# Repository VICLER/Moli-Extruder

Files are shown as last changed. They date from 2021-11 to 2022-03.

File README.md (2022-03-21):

<h1 align="center">Moli Extruder</h1>
<p align="center">The most lightweight dual drive filament extruder based on BMG drive gears with 5:1 gear ratio.</p>

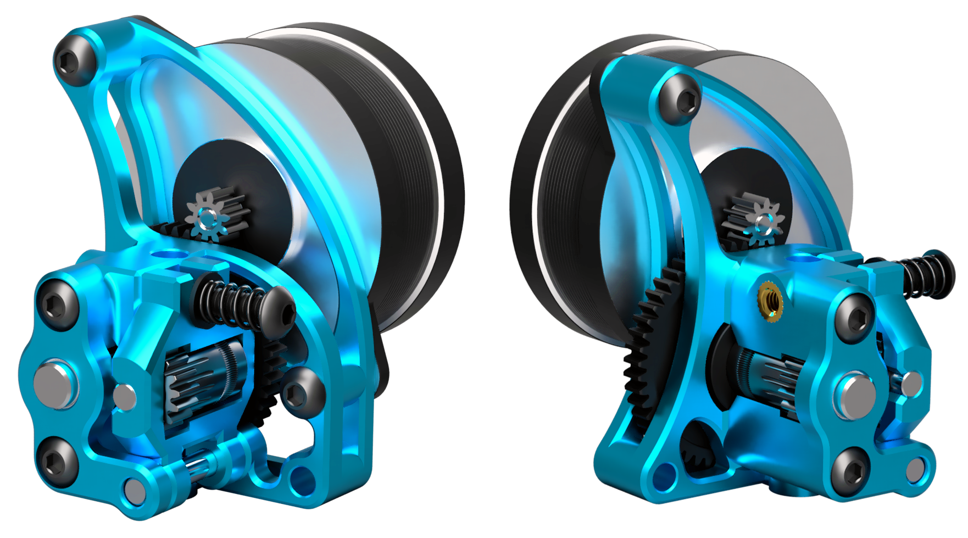
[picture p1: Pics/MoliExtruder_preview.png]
PROJECT_PHOTO


## Specs
- Outer dimensions (w/o motor) L×W×H: 37.2 × 28.2 × 48.7 (mm)
- Filament diameter: 1.75 mm
- Max feedrate: ~1200 mm/min
- Max flowrate: ~48 mm³/s
- Volume of all printed parts: ~6.14 cm³ (~63% less than Sailfin, ~55% less than Sherpa mini, ~52% less than HextrudORT and ~30% less than Sherpa micro extruder)
- Weight: <=25g (w/o motor). With LDO-36STH17-1004AHG: <=95g
- Mirrored version is also available

There are two versions for different types of BMG drive shaft available. They differ slightly, so check the measurements of your drive shaft and compare it with the CAD model  

This is a BETA release. Files, instructions, and other stuff might change!

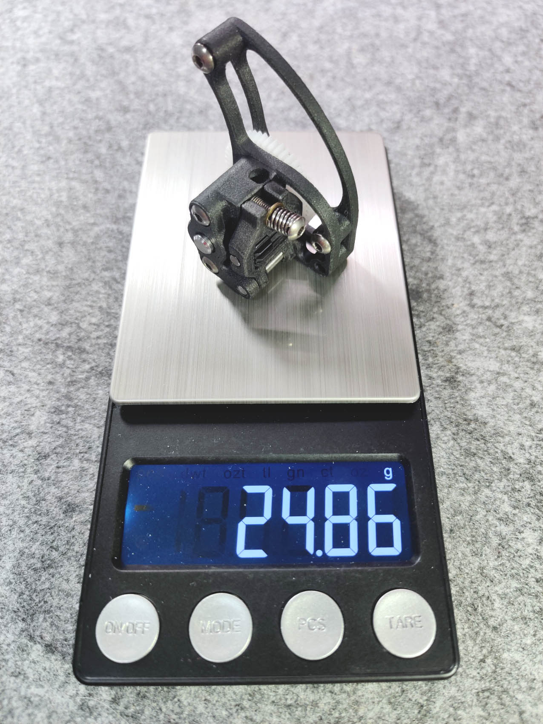
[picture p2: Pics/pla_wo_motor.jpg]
weight


## BOM
This extruder is designed to use Sherpa mini spare parts. Originally they are BMG dual drive extruder parts, but with one 3×20mm shaft instead of 3×32mm shaft. So you can buy original BMG dual drive spare parts and cut off the shaft by yourself.

- (1×) Motor [LDO-36STH 17/20mm](https://www.aliexpress.com/item/1005002899860754.html)  
- (1×) BMG internals [Recommended from Trianglelabs Store](https://www.aliexpress.com/item/4000021186440.html) or [Mellow Store](https://www.aliexpress.com/item/1005002254569027.html) (or [a bit cheaper, but not tested](https://www.aliexpress.com/item/1005003334389217.html))
- (1×) M3×18mm(optimal) or M3×16 screw
- (2×) M3×12mm screw
- (2×) M3×6mm  screw
- (1×) washer for M3 screw
- (1×) [compession spring](https://www.aliexpress.com/item/4000626844807.html). Wire diameter 0.7mm, outer diameter 5mm, length 10mm

## Print settings
Material: ABS or some high temp resistant filaments (like Extrudr Green-TEC PRO)  
Nozzle: <=0.4mm   
Walls:  3  
Infil:  100%  
Layer height: 0.1mm (optional 0.2mm first layer)

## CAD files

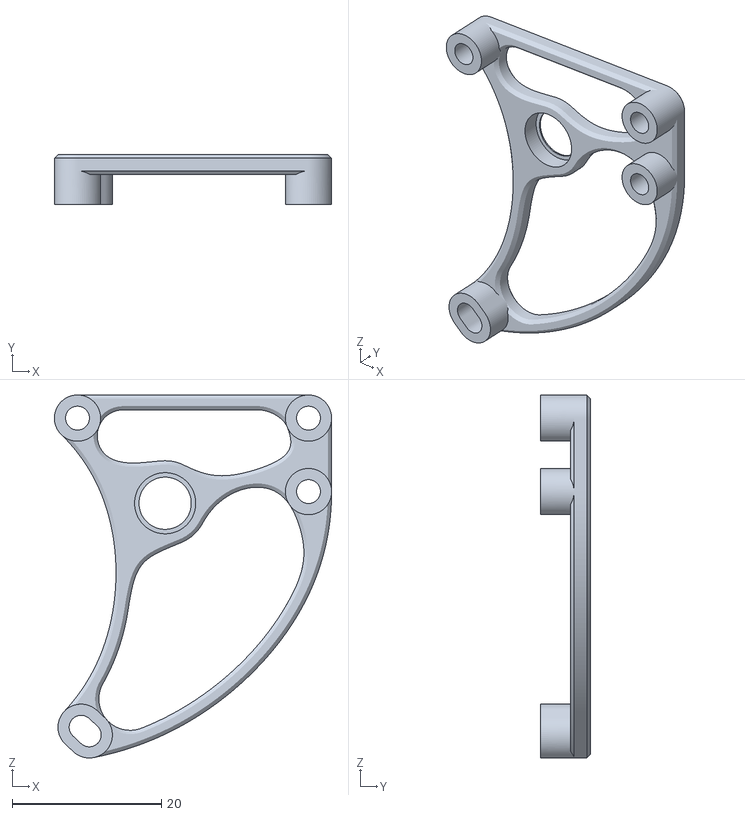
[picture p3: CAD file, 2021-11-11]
STL/BMG Fysetc Shaft/Mirror/MoliExtuder_bottom_mirror.stl
37.2 x 6.70 x 48.7

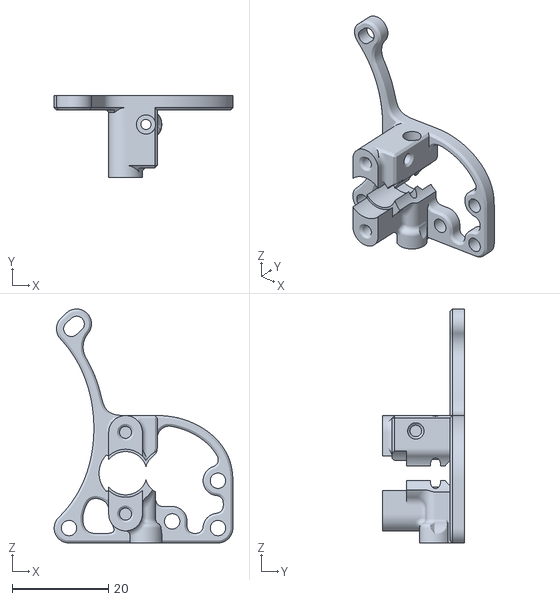
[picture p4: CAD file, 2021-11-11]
STL/BMG Fysetc Shaft/MoliExtruder_middle.stl
37.2 x 17.0 x 48.7

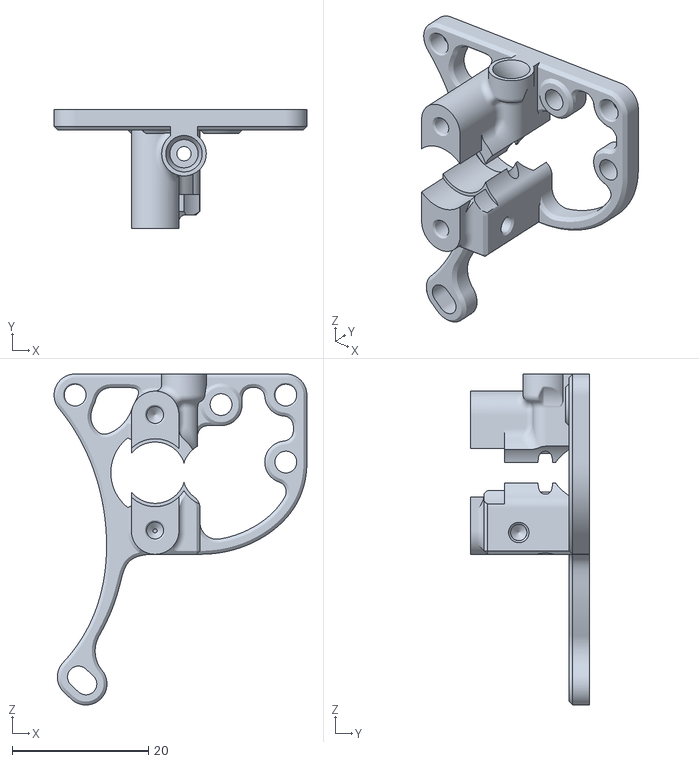
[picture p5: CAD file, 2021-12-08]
STL/BMG Shaft/Mirror/MoliExtruder_middle_mirror.stl
37.2 x 17.5 x 48.7

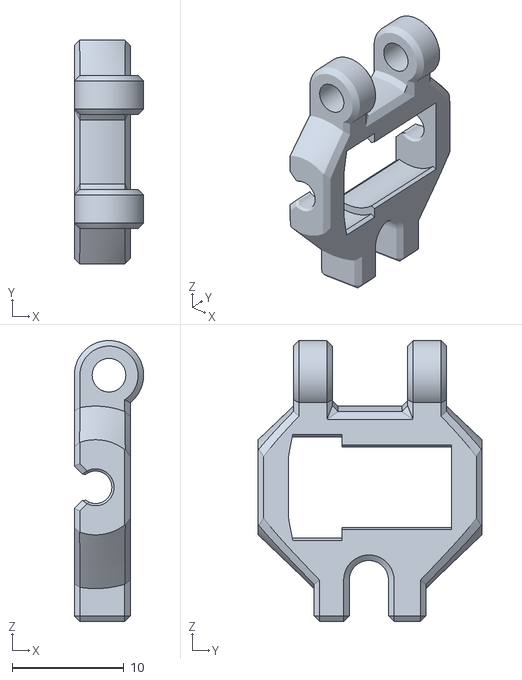
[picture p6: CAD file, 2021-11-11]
STL/BMG Fysetc Shaft/Mirror/MoliExtruder_arm_mirror.stl
6.20 x 20.0 x 25.1

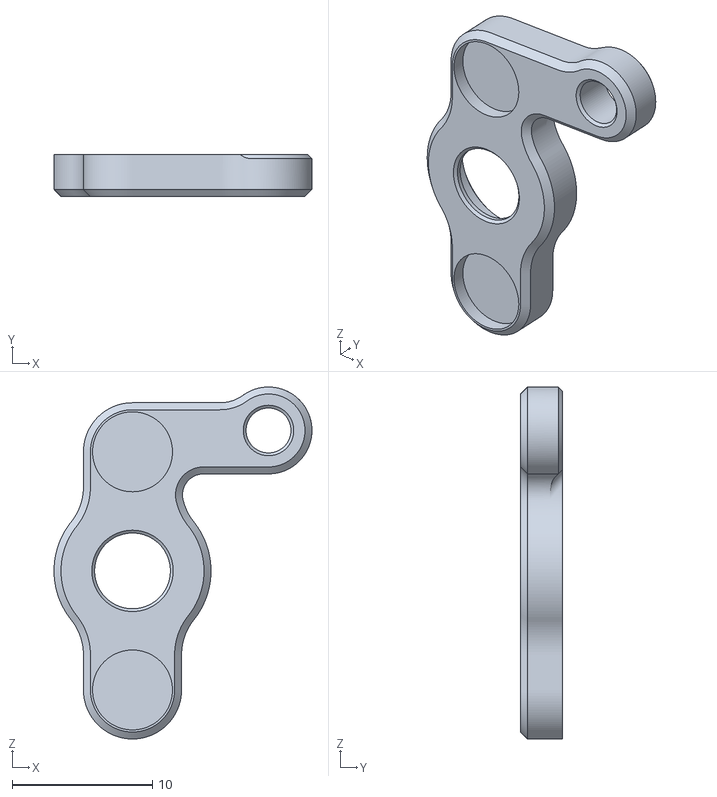
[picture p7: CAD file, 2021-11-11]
STL/BMG Shaft/Mirror/MoliExtruder_top_mirror.stl
18.4 x 3.00 x 25.1

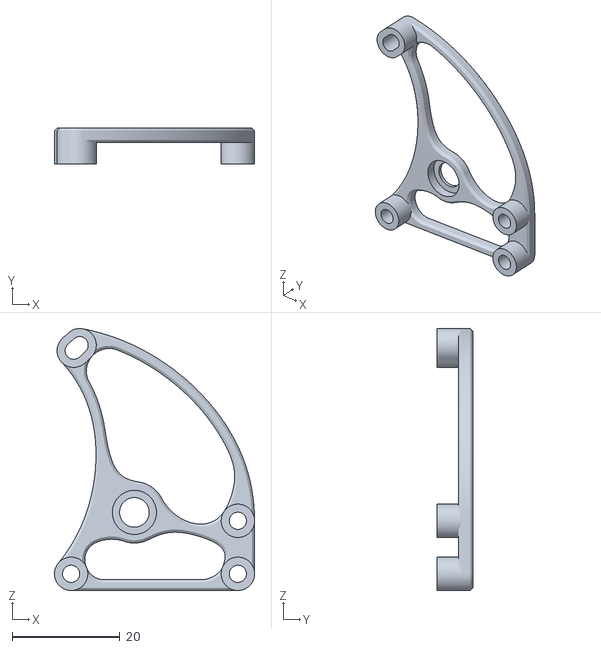
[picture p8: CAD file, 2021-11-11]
STL/BMG Shaft/MoliExtruder_bottom.stl
37.2 x 6.70 x 48.7

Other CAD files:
STL/BMG Shaft/MoliExtruder_middle.stl
STL/BMG Fysetc Shaft/MoliExtuder_bottom.stl
STL/BMG Shaft/Mirror/MoliExtruder_arm_mirror.stl
STL/BMG Shaft/MoliExtruder_arm.stl
STL/BMG Fysetc Shaft/Mirror/MoliExtruder_middle_mirror.stl
STL/BMG Fysetc Shaft/MoliExtruder_arm.stl
STL/BMG Fysetc Shaft/Mirror/MoliExtruder_top_mirror.stl
STL/BMG Fysetc Shaft/MoliExtruder_top.stl
STL/BMG Shaft/Mirror/MoliExtruder_bottom_mirror.stl
STL/BMG Shaft/MoliExtruder_top.stl

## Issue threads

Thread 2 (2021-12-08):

Extra ledge blocks the gear

fixid-pub, 2021-12-08:
File: STEP/BMG Shaft/Mirror/Middle
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

VICLER, 2021-12-08:
fixed!

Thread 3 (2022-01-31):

No screw holes in the top part

dolinenkov, 2022-01-31:
Hi!
It seems the top part is missing two screw holes.
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

VICLER, 2022-02-05:
Hi, it's not an issue, but thin support layer. It was designed to print front face down on printing surface.

Closed 2022-02-12.

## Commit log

2021-12-08 fix mirrored middle part
    [MoliExtruder_middle_mirror.stl]
2022-03-22 upd v2
    added heat insert
